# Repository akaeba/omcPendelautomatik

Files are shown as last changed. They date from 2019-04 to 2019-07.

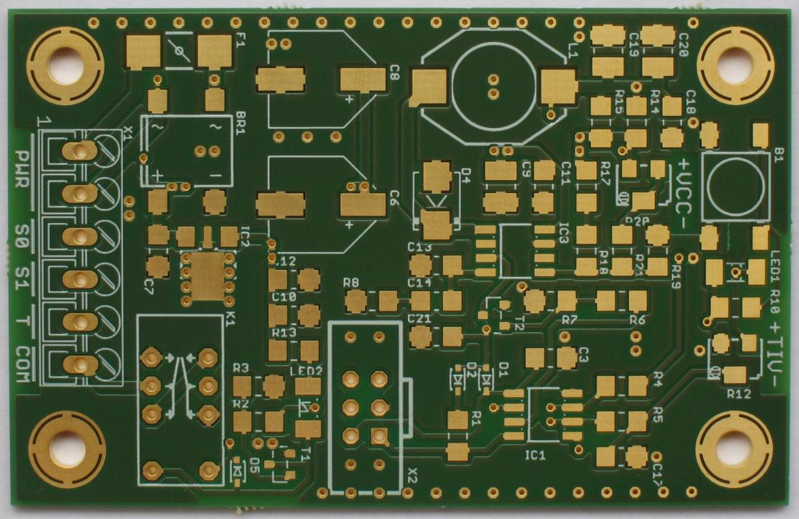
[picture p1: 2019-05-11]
98_pic/pcb_top.jpg

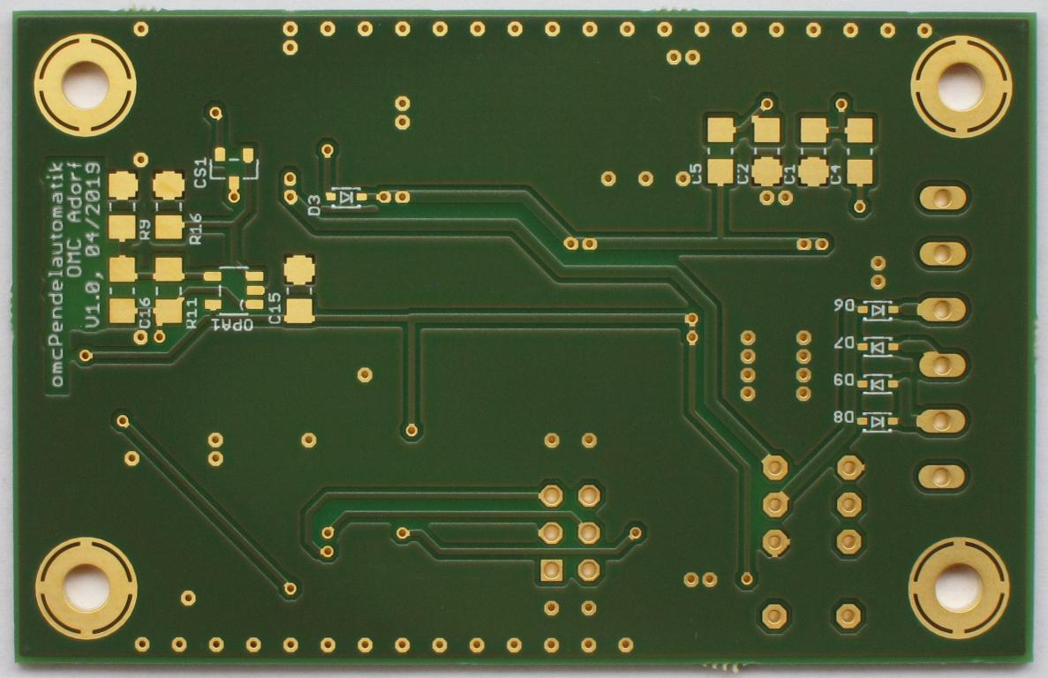
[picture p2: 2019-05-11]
98_pic/pcb_bottom.jpg

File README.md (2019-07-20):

# omcPendelautomatik
Circuit to drive a model train cyclic from one station to the other and back.

## Schematic

### Current Supervision

#### Current sensing and high-to-low conversion
The current sensor measures the voltage drop over an 0.5R shunt resistor. The high to low side voltage translation
is realized by [ZXCT1009](https://www.diodes.com/assets/Datasheets/ZXCT1009.pdf). According to the datasheet causes 
100mV voltage difference a output current of 1mA. Follows for V<sub>OUT</sub>:

V_{out} = I_{VCC} \cdot R_{SENSE}} \cdot \frac{1mA}{100mV} \cdot R_{out}

with R<sub>SENSE</sub>=0.5 and R<sub>OUT</sub>=200:

I_{VCC}[A]=V_{OUT}[V]

#### Opamp signal conditioning
The current sensors output voltage is processed by an band-limited operational amplifier

##### Amplification
The following can be noted as a starting point:

\Large -I_1=\frac{V_I}{R_1}
\Large I2=\frac{V_O-V_I}{R_2}
\Large 0=I_2-I_1

All three equations inserted into each other:

\Large \frac{V_O-V_I}{R_2}-\frac{V_I}{R_1}

For the amplification follows:

\Large V_O=V_I\Bigl(1+\frac{R_2}{R_1}\Bigr)

##### Band limit
A band limitation of the operational amplifier guarantees a good SNR and ADC resolution. An capacitor in parallel to R<sub>2</sub> limits the amplification.
The [Amplification](#Amplification) extended with an expression of the capacitive resistance follows:

\Large V_O=V_I\Bigl(1+\frac{R_2||\frac{1}{\omega C}}{R_1}\Bigr)

After short calculation and solving the parallel operator:

\Large V_O=V_I\Bigl(1+\frac{R_2}{R_1(1+\omega CR_2)}\Bigr)

Using the -3dB criteria

\frac{1}{\sqrt{2}}

Follows

\frac{1}{\sqrt{2}}=\frac{R_2}{R_1(1+\omega CR_2})

Solved for C

\boxed{C=\frac{\sqrt{2}R_2-R_1}{\omega R_1 R_2}}

## Used Tools
* Eagle 7.7

## Libraries
* Eagle:
    * [omcEagleLib](https://github.com/gallioleo/omcEagleLib)

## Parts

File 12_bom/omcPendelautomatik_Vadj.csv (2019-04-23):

Qty | Order | Distributor | Reference | VALUE | Description
1 | SMD 1/4W 0,0 | Reichelt | R17 | 0R | YAGEO RC1206 - General Purpose Chip Resistors
2 | X7R-G1206 100N | Reichelt | C15, C21 | 100n/50V | X7R Ceramic Capacitors
5 | X7R-G1206 100N | Reichelt | C3, C10, C11, C17, C18 | 100n/50V | X7R Ceramic Capacitors
1 | 44W-10K | Reichelt | R12 | 10K | Model 44 - Cermet Trimming Potentiometer - TT Electronics
3 | SMD 1/4W 10K | Reichelt | R2, R6, R9 | 10K | YAGEO RC1206 - General Purpose Chip Resistors
4 | X7R-G1206 10N | Reichelt | C1, C2, C4, C5 | 10n/50V | X7R Ceramic Capacitors
1 | X7R-G1210 10 | Reichelt | C9 | 10µ/35V | X7R Ceramic Capacitors
2 | VF 150/35 P-F | Reichelt | C6, C8 | 150µ/35V | Aluminum Electrolytic Capacitors
4 | SMD 1/4W 1,0K | Reichelt | R4, R5, R10, R13 | 1K | YAGEO RC1206 - General Purpose Chip Resistors
2 | SMD 1/4W 1,0 | Reichelt | R14, R15 | 1R | YAGEO RC1206 - General Purpose Chip Resistors
1 | SMD 1/4W 200 | Reichelt | R16 | 200R | YAGEO RC1206 - General Purpose Chip Resistors
1 | NPO-G1206 220P | Reichelt | C13 | 220p/50V | NP0 Surface-Mount Ceramic Multilayer Capacitors
1 | SMD 1/4W 22K | Reichelt | R1 | 22K | YAGEO RC1206 - General Purpose Chip Resistors
1 | X7R-G1206 22N | Reichelt | C14 | 22n/50V | X7R Ceramic Capacitors
1 | WSL 6G | Reichelt | X2 | 2X3 | Box Header 2X3
1 | NPO-G1206 2,2N | Reichelt | C16 | 2n2/50V | NP0 Surface-Mount Ceramic Multilayer Capacitors
2 | X7R-G1206 2,2/50 | Reichelt | C7, C12 | 2µ2/50V | X7R Ceramic Capacitors
1 | L-PISM 33µ | Reichelt | L1 | 33µ | PISM - SMD Power Inductors
1 | SMD 1/4W 39K | Reichelt | R11 | 39K | YAGEO RC1206 - General Purpose Chip Resistors
1 | SMD 1/4W 3,3K | Reichelt | R19 | 3K3 | YAGEO RC1206 - General Purpose Chip Resistors
1 | SMD 1/4W 47K | Reichelt | R18 | 47K | YAGEO RC1206 - General Purpose Chip Resistors
2 | X5R-G1210 47 | Reichelt | C19, C20 | 47µ/16V | X5R Ceramic Capacitors
2 | SMD 1/4W 4,7K | Reichelt | R8, R21 | 4K7 | YAGEO RC1206 - General Purpose Chip Resistors
1 | 44W-50K | Reichelt | R20 | 50K | Model 44 - Cermet Trimming Potentiometer - TT Electronics
2 | SMD 1/4W 56K | Reichelt | R3, R7 | 56K | YAGEO RC1206 - General Purpose Chip Resistors
1 | TS 78L05 ACY | Reichelt | IC2 | 7805 | STMicroelectronics - L78L - Positive voltage regulators
2 | BSS 138 SMD | Reichelt | T1, T2 | BSS138 | BSS 138 - N-Channel Logic Level Enhancement Mode Field Effect Transistor
1 | SMD DB1A70 | Reichelt | BR1 | DB102S | DIL Rechtifier - 1.0A Single-Phase Glass Passivated Bridge Rectifier
1 | TASTER 9314 | Reichelt | B1 | JTP1138/4.3 | TACT SWITCH - JTP 1138
1 | L 5970 D | Reichelt | IC3 | L5970D | STMicroelectronics - L5970D - Up to 1A step down switching regulator
1 | MBRS 240 SMD | Reichelt | D4 | MBRS240 | MBRS2X0 - 2A Schottky Power Rectifier
1 | MCP 6401T-E/OT | Reichelt | OPA1 | MCP6401 | MCP6401 - 1 MHz, 45 µA Op Amps - Microchip
1 | NA 05W K | Reichelt | K1 | NA-5V | Fujitsu NA - Minature Relay - 2 Poles - 1 to 2A
1 | PIC 12F675-I/SN | Reichelt | IC1 | PIC12F675 | PIC12F675 - 8-Pin FLASH-Based 8-Bit CMOS Microcontrollers
8 | PMEG 4010BEA NXP | Reichelt | D1, D2, D3, D5, D6, D7, D8, D9 | PMEG4010 | PMEGXX10 - 1A very low VF MEGA Schottky barrier rectifier - NXP
1 | AKL 086-06 | Reichelt | X1 | RT034 Typ 086 | Screw solder terminal - X06
1 | SMD-LED 1206 RT | Reichelt | LED1 | Red | LED Monochromatic
1 | OMT 125 0,5A | Reichelt | F1 | T 0A5 | OMT - Non resettable SMD Fuse
1 | SMD-LED 1206 GE | Reichelt | LED2 | Yellow | LED Monochromatic
1 | ZXCT 1009FTA | Reichelt | CS1 | ZXCT1009 | ZXCT1009 - HIGH-SIDE CURRENT MONITOR

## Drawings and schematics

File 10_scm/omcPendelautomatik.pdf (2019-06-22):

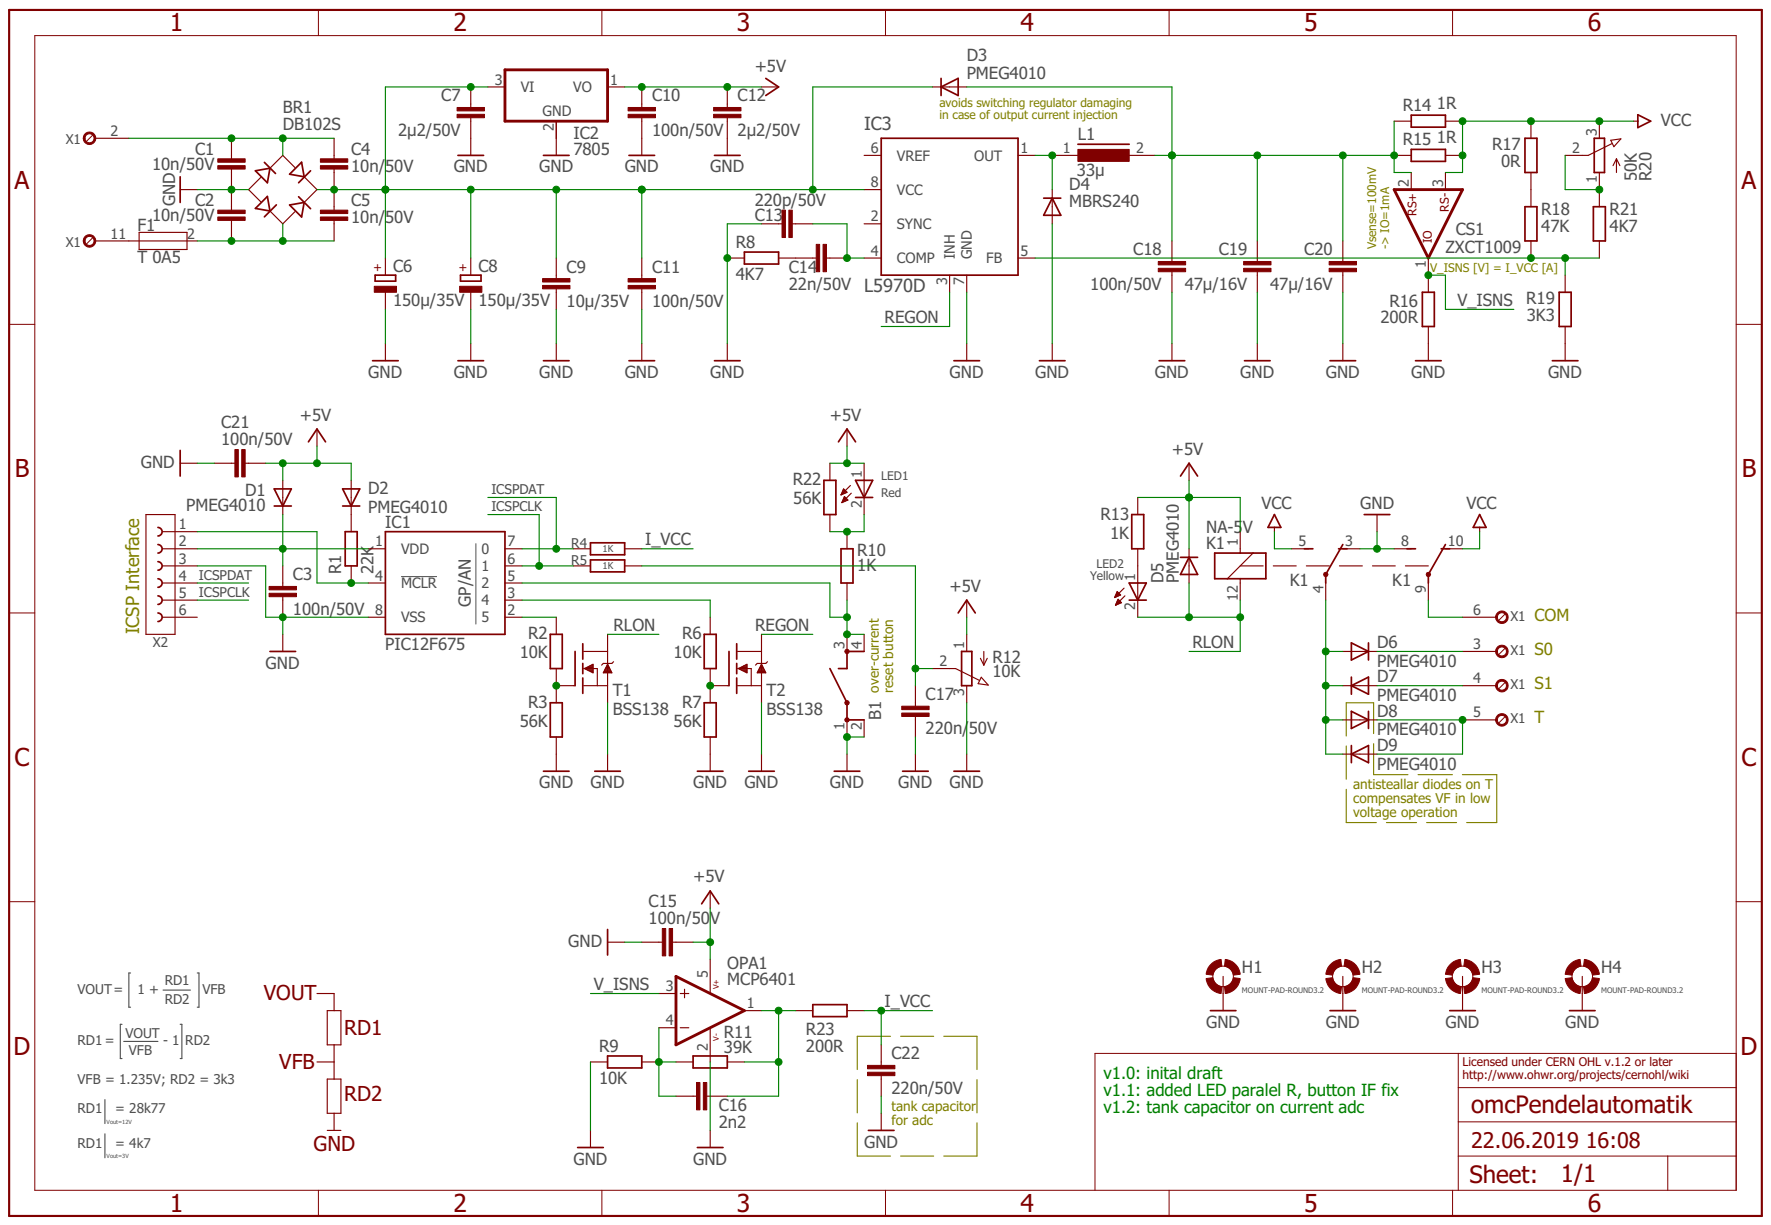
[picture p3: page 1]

avoids switching regulator damaging
in case of output current injection

over-current reset button tank capacitor

antisteallar diodes on T
compensates VF in low
voltage operation

Licensed under CERN OHL v.1.2 or later http://www.ohwr.org/projects/cernohl/wiki omcPendelautomatik

v1.1: added LED paralel R, button IF fix v1.0: inital draft v1.2: tank capacitor on current adc

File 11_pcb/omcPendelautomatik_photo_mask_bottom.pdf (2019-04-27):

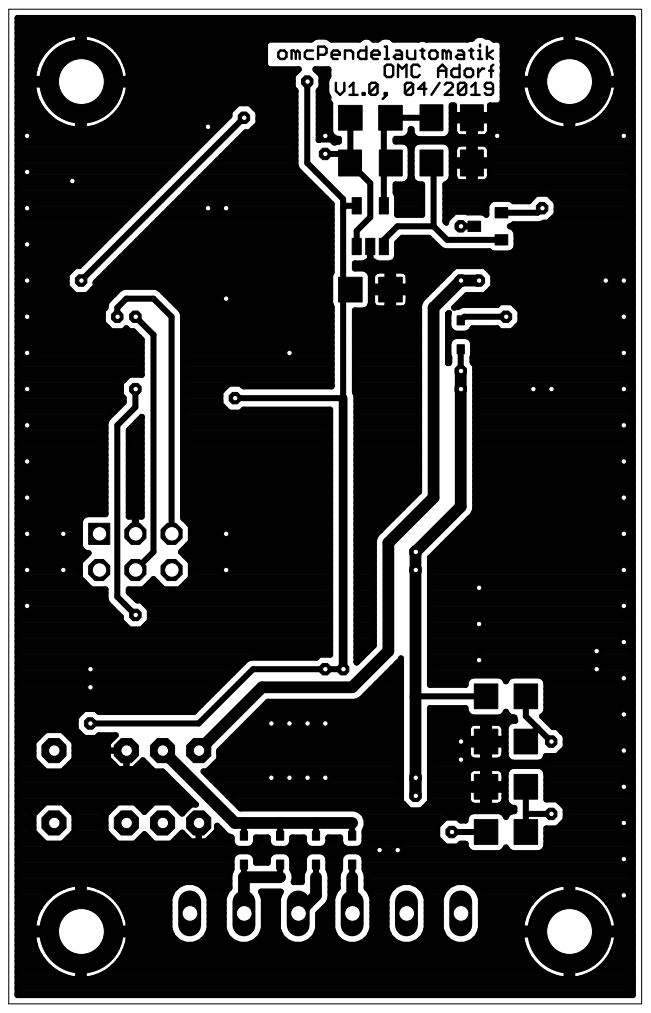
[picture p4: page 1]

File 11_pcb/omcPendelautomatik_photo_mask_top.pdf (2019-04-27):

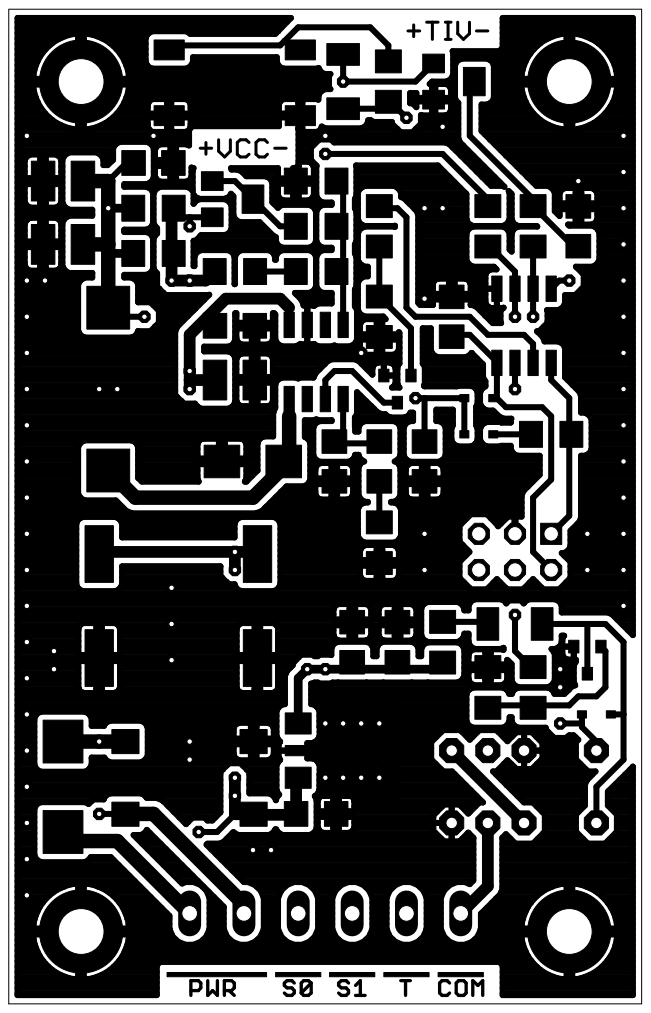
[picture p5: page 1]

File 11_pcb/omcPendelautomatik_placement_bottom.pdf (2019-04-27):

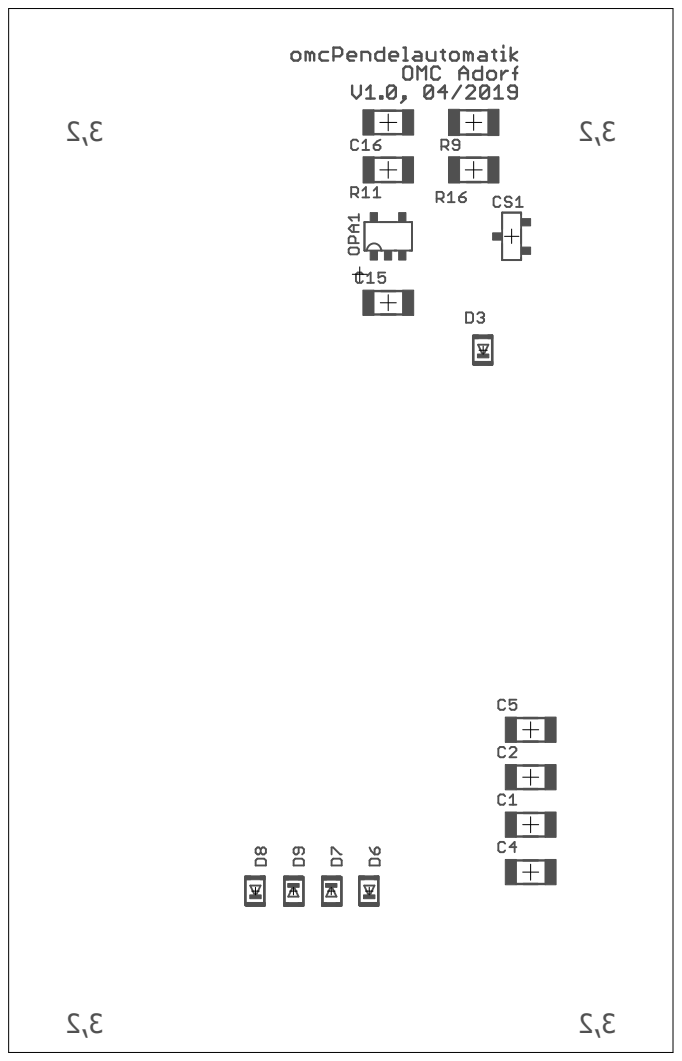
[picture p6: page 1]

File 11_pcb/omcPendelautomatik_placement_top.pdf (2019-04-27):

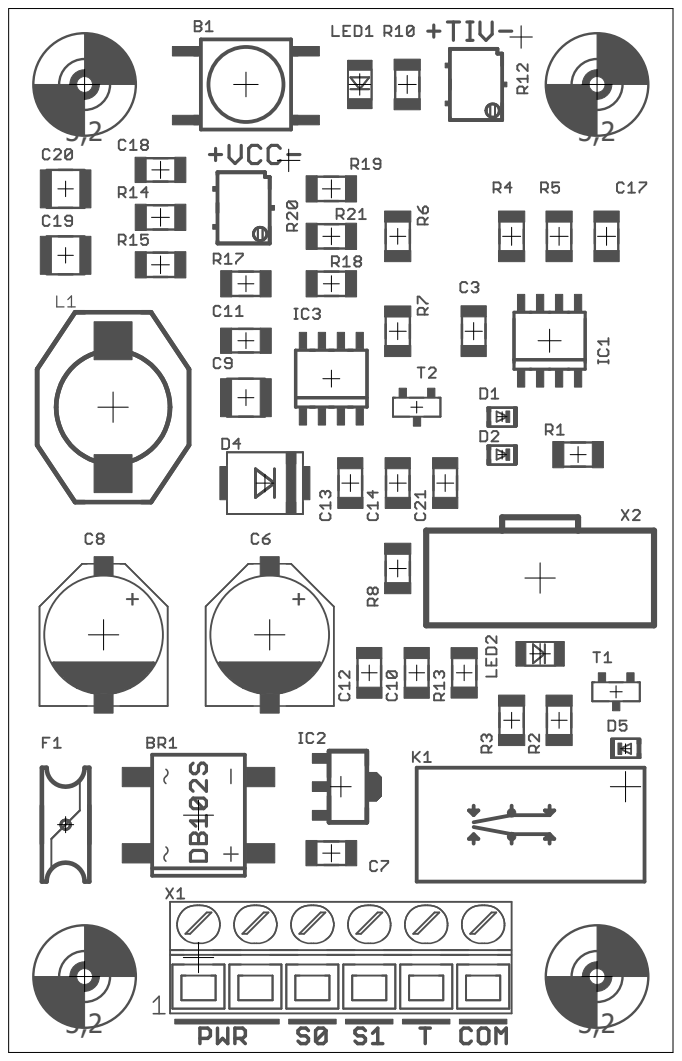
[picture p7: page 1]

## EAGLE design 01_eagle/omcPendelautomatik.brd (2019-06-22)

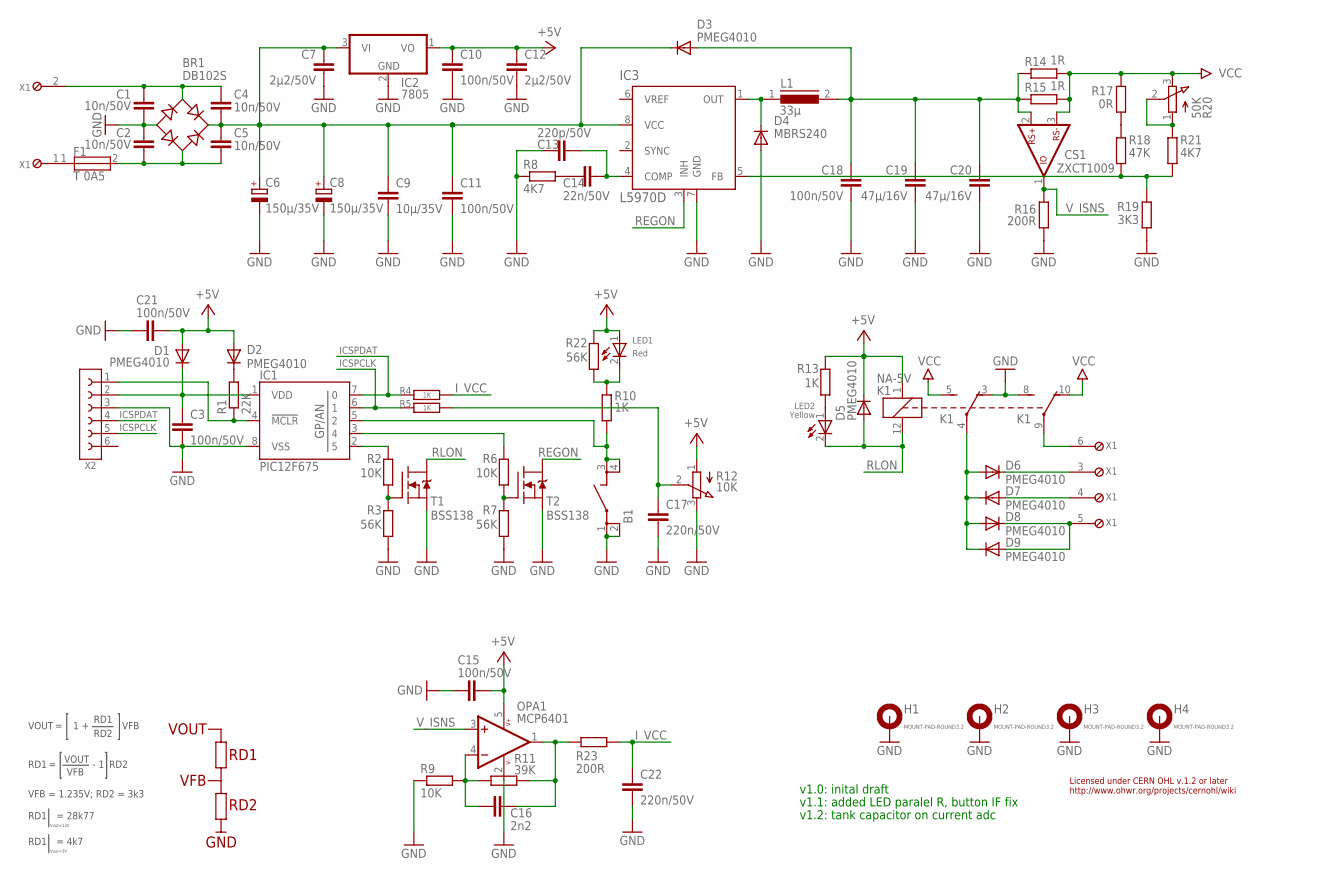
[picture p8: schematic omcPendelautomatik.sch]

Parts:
B1: JTP1138/4.3; SMD_X4_11X6
BR1: DB102S; DBS
C1, C2, C4, C5: 10n/50V; 1206
C3, C10, C11, C15, C18, C21: 100n/50V; 1206
C6, C8: 150µ/35V; PANF
C7, C12: 2µ2/50V; 1206
C9: 10µ/35V; 1210
C13: 220p/50V; 1206
C14: 22n/50V; 1206
C16: 2n2; 1206
C17, C22: 220n/50V; 1206
C19, C20: 47µ/16V; 1210
CS1: ZXCT1009; SOT23
D1, D2, D3, D5, D6, D7, D8, D9: PMEG4010; SOD323
D4: MBRS240; DO214AA
F1: T 0A5; OMT125
H1, H2, H3, H4: MOUNT-PAD-ROUND3.2; 3,2-PAD
IC1: PIC12F675; SOIC08
IC2: 7805; SOT89W
IC3: L5970D; SOIC08
K1: NA-5V; THT_5M08M_5M08M_2M54M
L1: 33µ; PISM
LED1: Red; LED3216
LED2: Yellow; LED3216
OPA1: MCP6401; SOT23-5
R1: 22K; 1206
R2, R6, R9: 10K; 1206
R3, R7, R22: 56K; 1206
R4, R5, R10, R13: 1K; 1206
R8, R21: 4K7; 1206
R11: 39K; 1206
R12: 10K; TTM44W
R14, R15: 1R; 1206
R16, R23: 200R; 1206
R17: 0R; 1206
R18: 47K; 1206
R19: 3K3; 1206
R20: 50K; TTM44W
T1, T2: BSS138; SOT23
X1: RT034 Typ 086; RT03406T086
X2: 2X3; BOXHD-06-2.54-S

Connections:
+5V: C10.1, C12.1, C15.2, C21.2, D1.A, D2.A, D5.C, IC2.1 (VO), K1.1 (2), LED1.1 (A), OPA1.5 (V+), R12.1 (A), R13.2, R22.2
GND: B1.1, B1.2, BR1.-, C1.2, C2.1, C3.2, C6.CN (-), C7.2, C8.CN (-), C9.2, C10.2, C11.2, C12.2, C13.1, C15.1, C17.2, C18.2, C19.2, C20.2, C21.1, C22.2, D4.A, H1.B3,2, H2.B3,2, H3.B3,2, H4.B3,2, IC1.8 (VSS), IC2.2 (GND), IC2.4 (GND), IC3.7 (GND), K1.3 (O), K1.8 (S), OPA1.2 (V-), R3.1, R7.1, R8.1, R9.1, R12.3 (E), R16.1, R19.1, T1.2 (S), T2.2 (S), X2.3
ICSPCLK: IC1.6 (1), R5.1, X2.5
ICSPDAT: IC1.7 (0), R4.1, X2.4
I_VCC: C22.1, R4.2, R23.1
unnamed: D4.C, IC3.1 (OUT), L1.1
unnamed: R20.1 (A), R20.2 (S), R21.2
unnamed: C13.2, C14.1, IC3.4 (COMP)
unnamed: C14.2, R8.2
unnamed: R2.1, R3.2, T1.1 (G)
unnamed: BR1.+, C4.2, C5.1, C6.CP (+), C7.1, C8.CP (+), C9.1, C11.1, D3.C, IC2.3 (VI), IC3.8 (VCC)
unnamed: C3.1, D1.C, IC1.1 (VDD), X2.2
unnamed: F1.1, X1.1
unnamed: IC3.5 (FB), R18.1, R19.2, R21.1
unnamed: IC1.4 (!MCLR!), R1.1, X2.1
unnamed: D2.C, R1.2
unnamed: IC1.2 (5), R2.2
unnamed: R6.1, R7.2, T2.1 (G)
unnamed: IC1.3 (4), R6.2
unnamed: LED2.1 (A), R13.1
unnamed: R17.1, R18.2
unnamed: BR1.AC1, C1.1, C4.1, X1.2
unnamed: D6.C, X1.3
unnamed: C17.1, R5.2, R12.2 (S)
unnamed: C16.1, OPA1.4 (-IN), R9.2, R11.1
unnamed: D7.A, X1.4
unnamed: D6.A, D7.C, D8.A, D9.C, K1.4
unnamed: BR1.AC2, C2.2, C5.2, F1.2
unnamed: K1.9, X1.6
unnamed: B1.3, B1.4, IC1.5 (2), R10.1
unnamed: D8.C, D9.A, X1.5
unnamed: LED1.2 (C), R10.2, R22.1
unnamed: C16.2, OPA1.1 (OUT), R11.2, R23.2
REGON: IC3.3 (INH), T2.3 (D)
RLON: D5.A, K1.12 (1), LED2.2 (C), T1.3 (D)
VCC: CS1.3 (-RS), K1.5 (S), K1.10 (O), R14.2, R15.2, R17.2, R20.3 (E)
VOUT: C18.1, C19.1, C20.1, CS1.2 (+RS), D3.A, L1.2, R14.1, R15.1
V_ISNS: CS1.1 (IOUT), OPA1.3 (+IN), R16.2

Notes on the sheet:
GND
VFB
VOUT
RD1
RD2
1 +
VFB = 1.235V; RD2 = 3k3
= 28k77
- 1
Vout=12V
= 4k7
Vout=3V
Licensed under CERN OHL v.1.2 or later http://www.ohwr.org/projects/cernohl/wiki
v1.1: added LED paralel R, button IF fix
v1.0: inital draft
v1.2: tank capacitor on current adc

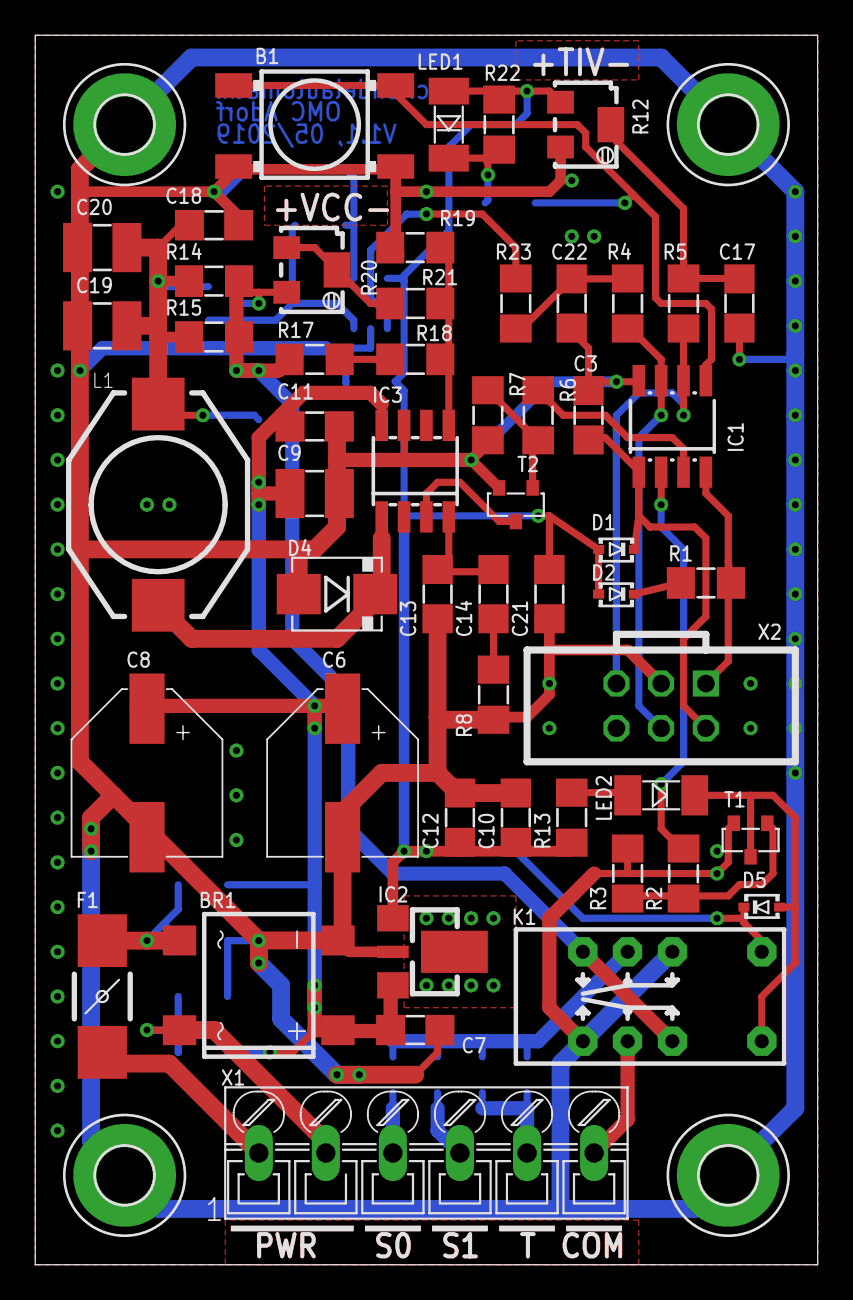
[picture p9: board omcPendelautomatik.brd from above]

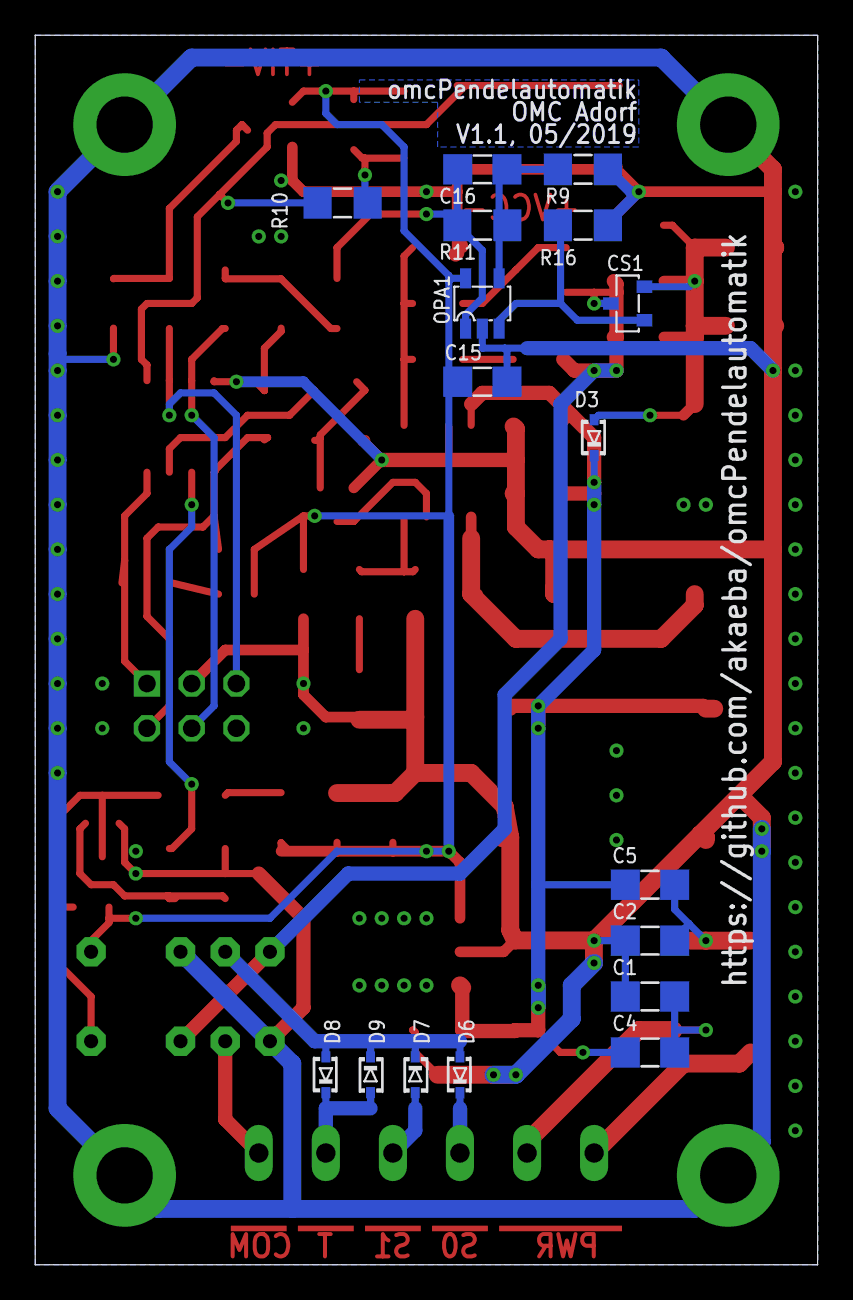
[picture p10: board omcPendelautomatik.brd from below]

Board: 2 copper layers, 44.5 x 69.8 mm, 74 parts (17 on the bottom side), 38 nets.

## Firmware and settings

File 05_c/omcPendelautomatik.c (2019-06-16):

/******************************************************************************
*  @copyright  GPLv3
*  Company     OMC Adorf
*  Address     Markt 35b, 08626 Adorf
*
*  @file       omcPendelautomatik.c
*  @author     Andreas Kaeberlein <andreas.kaeberlein@web.de>
*  @date       May 2, 2019
*  @version    1.0
*
*  @brief      FW Pendelautomatik
*
*  Implements behaviour Pendelautomatik
*
*******************************************************************************/


/** Includes **/
/* standard libs */
#include <stdint.h>
/* self */
#include "omcPendelautomatik.h"



/**
 *  mcu_init
 *    intializes MCU, port, timers, adcs...
 */
int mcu_init()
{
    /* Configure IO */
    GPIO   = 0;                       // all GPIOs drive zero
    GPIO   |= GP2;                    // Red OC LED is off
    TRISIO = IO_ALL_INPUT;            // All IOs are Input
    TRISIO &= ~(TRISIO4 | TRISIO5);   // GPIO4/5 is output

    /* Configure ADC */
    ADCON0 = 0;                           // prepare for OR
    ADCON0 |= (ADC_ADFM_LEFT << ADFM);    // ADC word alignment
    ADCON0 |= (ADC_VCFG_VDD << VCFG);     // ADC reference is VDD
    ANSEL  = 0;                           // clear register
    ANSEL  |= ( ANS0 | ANS1 );            // GP0 and GP1 analog input
    ANSEL  |= ADC_FOSC_64;                // Tconv = 64 * 1 / 8 MHz = 8us
    ADRESH = 0;                           // clear
    ADRESL = 0;                           //
     
    /* configure timer0 for 1ms interrupt */
    TMR0       = 0;         // clear timer
    OPTION_REG &= ~T0CS;    // Internal instruction cycle clock (CLKOUT)
    OPTION_REG |= PSA;      // Prescaler is assigned to the WDT
     
    /* configure IRQ */
    INTCON = 0;        // all interrupts disable
    INTCON |= T0IE;    // timer0 interrupt enable, required for 1ms timing normal
    INTCON |= GIE;     // all unmasked IRQ enabled
     
    /* gracefull end */
    return 0;
}



/**
 *  handle_init
 *    intializes common used storage handle
 */
int handle_init(tOmcPendelautomatik *self)
{
    /* init variable */
    self->uint8TmrDiv = 0;
    self->int16TmrFrac = 0;
    self->uint32Time_ms = 0;
    self->uint8AdcBuf0[0] = 0;
    self->uint8AdcBuf0[1] = 0;
    self->uint8AdcBuf0[2] = 0;
    self->uint8AdcBuf1[0] = 0;
    self->uint8AdcBuf1[1] = 0;
    self->uint8AdcBuf1[2] = 0;
    self->uint8CurIL = 0;
    self->uint8CurTi = 0;

    /* gracefull end */
    return 0;
}



/**
 *  shift_value
 *    shift value one position down in array
 */
int shift_value(uint8_t val[], uint8_t len)
{
    /** Variables **/
    uint8_t    i;    // iterator
    
    /* shift value down */
    for ( i = 1; i < len; ++i ) {
        val[i] = val[i-1];
    }
    
    /* gracefull end */
    return 0;
}



/**
 *  interrupt
 *    interrupt service routine
 */
void interrupt(tOmcPendelautomatik *self)
{
    /* disable all unmasked interrupt */
    INTCON &= ~GIE;
    
    /* TMR0 IRQ? */
    if ( INTCON.T0IF ) {
        /* IRQ Flag */
        INTCON &= ~T0IF;    // clear interupt flag
        
        /* 1ms Timing Normal 
         * TMR0 (8bit) used, IRQ at overflow 0xFF -> 0x00
         * FOSC 8MHz
         * (1ms / ( (1 / 8 MHz) * TMR0 * 4 ) ) = 7,8125
         */
        self->uint8TmrDiv = self->uint8TmrDiv + 1;
        if ( (self->uint8TmrDiv == 7) && (self->int16TmrFrac >= 0) ) {
            self->uint8TmrDiv = 0;
            self->int16TmrFrac = self->int16TmrFrac - 8125;
            self->uint32Time_ms = self->uint32Time_ms + 1;
        } else if ( (self->uint8TmrDiv == 8) && (self->int16TmrFrac < 0) ) {
            self->uint8TmrDiv = 0;
            self->int16TmrFrac = self->int16TmrFrac + 1875;
            self->uint32Time_ms = self->uint32Time_ms + 1;
        }
        
        /* handle adc */
        if ( ! ADCON0.GO_NOT_DONE ) {
             /* Last Conversion from Chn0 performed 
              *   -> used for current measurement
              */
             if ( (ADCON0 & ADC_CHN_MSK) == ADC_CHN_0 ) {
                 /* update average current value */
                 self->uint16Temp = self->uint8AdcBuf0[0] + self->uint8AdcBuf0[1] + self->uint8AdcBuf0[2] + ADRESH;  // avearage with last four values
                 self->uint8CurIL = (uint8_t) (self->uint16Temp >> 2);                                               // four values, bit shift 2 for div4
                 shift_value(self->uint8AdcBuf0, sizeof(self->uint8AdcBuf0) / sizeof(self->uint8AdcBuf0[0]));        // drop last element
                 self->uint8AdcBuf0[0] = ADRESH;                                                                     // store current adc value
                 /* change input and start next conversion */
                 ADCON0 |= ADC_CHN_1;      // select Channel 1 as new analog input, prepare for time measurement
                 ADCON0 |= GO_NOT_DONE;    // start new conversion
                 
             /* Last Conversion from Chn1 performed 
              *   -> used for cycle time
              */
             } else if ( (ADCON0 & ADC_CHN_MSK) == ADC_CHN_1 ) {
                 /* update average current value */
                 self->uint16Temp = self->uint8AdcBuf1[0] + self->uint8AdcBuf1[1] + self->uint8AdcBuf1[2] + ADRESH;  // avearage with last four values
                 self->uint8CurTi = (uint8_t) (self->uint16Temp >> 2);                                               // four values, bit shift 2 for div4
                 shift_value(self->uint8AdcBuf1, sizeof(self->uint8AdcBuf1) / sizeof(self->uint8AdcBuf1[0]));        // drop last element
                 self->uint8AdcBuf1[0] = ADRESH;                                                                     // store current adc value
                 /* change input and start next conversion */
                 ADCON0 &= ~ADC_CHN_1;     // select Channel 0 as new analog input, prepare for current meas
                 ADCON0 |= GO_NOT_DONE;    // start new conversion
             }
        }
    }
    
    /* enable all unmasked IRQ */
    INTCON |= GIE;
}



/**
 *  wait_50ms
 *    waits 50ms
 */
int wait_50ms()
{
    delay_ms(50);
    return 0;
}



/**
 *  wait_500ms
 *    waits 500ms
 */
int wait_500ms()
{
    /** Variables **/
    uint8_t       i;
    
    /* call 50ms wait functions */
    for ( i = 0; i < 10; i++ ) {
        wait_50ms();
    }
    
    /* normal end */
    return 0;
}



/**
 *  handle_oc
 *    handles over current case, polls clear button
 */
int handle_oc()
{
     /** Variables */
     uint8_t   uint8ButtonNew = 1;
     uint8_t   uint8ButtonOld = 1;
     
     
      /* poll loop, over current clear button */
      while ( (uint8ButtonNew != uint8ButtonOld) && (uint8ButtonNew != 0) ) {
          /* read-out switch */
          TRISIO |= TRISIO2;                     // input
          delay_ms(1);                           // wait 1ms
          uint8ButtonOld = uint8ButtonNew;       // capture old value
          uint8ButtonNew = BUTTON_OC;            // read out value
          /* red LED */
          TRISIO &= ~TRISIO2;                    // output
          XLED_RED = OFF;                        // LED on
          delay_ms(9);                           // wait 9ms, 90% lumicity
      }
     
     /* graceful end */
     return 0;
}



/**
 *  main
 *    entry point
 */
int main() 
{
     /** Variables **/
     tOmcPendelautomatik myHandle;
     
     
     /* init */
     mcu_init();               // MCU
     handle_init(&myHandle);   // common storage element
     
     /* start cycling */
     IO_REG = ON;       // switch power supply on
     IO_RELAY = ON;     // switch relay on
     
     /* infinite loop */
     while(1) {
         /* check for direction change */
         if ( myHandle.uint32Time_ms > (UI_TIME_DIG_MS * myHandle.uint8CurTi) ) {
             myHandle.uint32Time_ms = 0;               // clear current time
             IO_REG = OFF;                             // disable regulator
             wait_50ms();                              // wait for regulator shutdown
             IO_RELAY = IO_RELAY ^ 0x1;                // toggle direction
             wait_50ms();                              // wait for relay
             IO_REG = ON;                              // enable power
         }
         
         /* check for over current */
         if ( myHandle.uint8CurTi > 25 ) {             // ToDO
             IO_REG = OFF;                             // stop current flow
             if ( 0 != handle_oc() ) {
                while(1) {                             // stuck finally, red LED blinks, leave with POR
                    IO_RELAY = OFF;
                    XLED_RED = OFF;
                    wait_500ms();
                    XLED_RED = ON;
                    wait_500ms();
                }
             }
             myHandle.uint32Time_ms = 0;               // clear current time, go one normally
             IO_REG = ON;                              // restore power supply
         }
     }
     
     /* graceful end */
     return 0;
}

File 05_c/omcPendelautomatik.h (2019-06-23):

/******************************************************************************
*  @copyright  GPLv3
*  Company     OMC Adorf
*  Address     Markt 35b, 08626 Adorf
*
*  @file       omcPendelautomatik.h
*  @author     Andreas Kaeberlein <andreas.kaeberlein@web.de>
*  @date       May 2, 2019
*  @version    1.0
*
*  @brief      FW Pendelautomatik
*
*  Implements behaviour Pendelautomatik
*
*******************************************************************************/


// Define Guard
#ifndef __OMC_PENDELAUTOMATIK_H
#define __OMC_PENDELAUTOMATIK_H

/**
 *  @defgroup CMACRO
 *  help macros for pre compiler
 *  @{
 */
#define pwrtwo(x) (1 << (x))
/** @} */   // CMACRO


/**
 *  @defgroup Help
 *  help defines
 *  @{
 */
#define UI_TIME_MIN_SEC      5                                                            /**<  UI: Minimal Time between direction change */
#define UI_TIME_MAX_SEC      180                                                          /**<  UI: Maximum Time between direction change */
#define UI_TIME_DIG_MS       (((UI_TIME_MAX_SEC - UI_TIME_MIN_SEC) * 1000 ) / pwrtwo(8))  /**<  UI: Time increment per measured digit     */
#define UI_OC_TRIP_MA        300                                                          /**<  UI: Fence for over current tripping       */
//#define UI_OC_TRIP_DIG

/** @} */   // UI


/**
 *  @defgroup ADC
 *  configures and controls the ADC
 *  @{
 */
#define ADC_FOSC_64     ( ADCS2 | ADCS1 )         /**<  ADC: Clock Divider =64, applied on ANSEL            */
#define ADC_CHN_IDX     2                         /**<  ADC: Analog Channel Select bits                     */
#define ADC_CHN_MSK     ( CHS1 | CHS0 )           /**<  ADC: sel channel selection bits, applied on ADCON   */
#define ADC_CHN_0       ( 0 << ADC_CHN_IDX )      /**<  ADC: Channel 00 (AN0)                               */
#define ADC_CHN_1       ( 1 << ADC_CHN_IDX )      /**<  ADC: Channel 01 (AN1)                               */
#define ADC_CHN_2       ( 2 << ADC_CHN_IDX )      /**<  ADC: Channel 02 (AN2)                               */
#define ADC_CHN_3       ( 3 << ADC_CHN_IDX )      /**<  ADC: Channel 03 (AN3)                               */
#define ADC_ADFM_LEFT   0                         /**<  ADC: A/D Result Formed, Left justified              */
#define ADC_ADFM_RIGHT  1                         /**<  ADC: A/D Result Formed, Right justified             */
#define ADC_VCFG_VREF   1                         /**<  ADC: Voltage Reference bit, VREF pin                */
#define ADC_VCFG_VDD    0                         /**<  ADC: Voltage Reference bit, VDD pin                 */
/** @} */   // ADC



/**
 *  @defgroup IO
 *  GPIO port control
 *  @{
 */
#define IO_ALL_INPUT ( TRISIO0 | TRISIO1 | TRISIO2 | TRISIO3 | TRISIO4 | TRISIO5 )     /**<  IO: GPIO pin configured as an input (tri-stated) */
#define IO_RELAY     GPIO.B5                                                           /**<  IO: Port Connected to Relay                      */
#define ON           1                                                                 /**<  IO: Relay is active                              */
#define OFF          0                                                                 /**<  IO: Relay is inactive                            */
#define IO_REG       GPIO.B4                                                           /**<  IO: Port Connected to Regulator                  */
#define XLED_RED     GPIO.B2                                                           /**<  IO: Feeds low active red LED                     */
#define BUTTON_OC    GPIO.B2                                                           /**<  IO: Reeds Over-current clear button out          */

/** @} */   // IO



/**
 *  @typedef tOmcPendelautomatik
 *
 *  @brief  data handle
 *
 *  programs data handle
 *
 *  @since  May 28, 2019
 *  @author Andreas Kaeberlein
 */
typedef struct tOmcPendelautomatik {
    uint8_t     uint8TmrDiv;               /**< divids from TMR0 IRQ to 1ms  */
    int16_t     int16TmrFrac;              /**< handles fracs to achieve MS  */
    uint32_t    uint32Time_ms;             /**< Time in ms steps             */
    uint8_t     uint8AdcBuf0[3];           /**< avering buffer for ADC input */
    uint8_t     uint8AdcBuf1[3];           /**< avering buffer for ADC input */
    uint16_t    uint16Temp;                /**< temporary variable           */
    uint8_t     uint8CurIL;                /**< current load current         */
    uint8_t     uint8CurTi;                /**< current cyclic time          */

} tOmcPendelautomatik;


/* C++ compatibility */
#ifdef __cplusplus
extern "C"
{
#endif // __cplusplus


/**
 *  @brief MCU init
 *
 *  intializes MCU, port, timers, adcs...
 *
 *  @retval         0                   OK
 *  @since          2019-06-16
 *  @author         Andreas Kaeberlein
 */
int mcu_init();


/**
 *  @brief init data handle
 *
 *  intializes common used storage handle
 *
 *  @param[in,out]  this                storage element
 *  @retval         0                   OK
 *  @since          2019-06-16
 *  @author         Andreas Kaeberlein
 */
int handle_init(tOmcPendelautomatik *self);


/**
 *  @brief shift value in array
 *
 *  shift value one position down in array
 *
 *  @param[in,out]  val                 array with values
 *  @param[in]      len                 length of provided array
 *  @return         int                 state
 *  @retval         0                   OK
 *  @since          2019-06-16
 *  @author         Andreas Kaeberlein
 */
int shift_value(uint8_t val[], uint8_t len);


/**
 *  @brief interrupt
 *
 *  interrupt service routine
 *
 *  @param[in,out]  this                storage element
 *  @since          2019-06-16
 *  @author         Andreas Kaeberlein
 */
void interrupt(tOmcPendelautomatik *self);


/** 
 *  @brief 50ms wait
 *
 *  calls prmitive routine to wait 50ms
 *
 *  @return         int                 state
 *  @retval         0                   OK
 *  @since          2019-06-16
 *  @author         Andreas Kaeberlein
 */
int wait_50ms();


/**
 *  @brief 500ms wait
 *
 *  calls wait_50ms routine and builds up 500ms wait
 *
 *  @return         int                 state
 *  @retval         0                   OK
 *  @since          2019-06-16
 *  @author         Andreas Kaeberlein
 */
int wait_500ms();


/**
 *  @brief handle_oc
 *
 *  handles over current case, polls clear button
 *
 *  @return         int                 state
 *  @retval         0                   OK
 *  @since          2019-06-16
 *  @author         Andreas Kaeberlein
 */
int handle_oc();


#ifdef __cplusplus
}
#endif // __cplusplus

#endif  // __OMC_PENDELAUTOMATIK_H

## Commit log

2019-04-01 omcPendelautomatik.sch -> intermediate commit, due architecture change
    [omcPendelautomatik.sch]
2019-04-07 omcPendelautomatik.sch -> intermediate commit -> changed from '555' timing normal to 'uC'
    [omcPendelautomatik.sch]
2019-04-11 omcPendelautomatik.sch -> initial draft schematic finished
    [omcPendelautomatik.sch]
2019-04-19 omcPendelautomatik -> Placement and routing main parts done -> schematic changes for routing
    [omcPendelautomatik.brd, omcPendelautomatik.sch]
2019-04-19 omcPendelautomatik.brd -> adjust silk print on top side
    [omcPendelautomatik.brd]
2019-04-21 omcPendelautomatik.brd -> adjust bottom side silk
    [omcPendelautomatik.brd]
2019-04-21 omcPendelautomatik -> symbol update -> added some vias to connect top/bottom ground plane
    [omcPendelautomatik.brd, omcPendelautomatik.sch]
2019-04-22 omcPendelautomatik.brd -> added Polygon to avoid thermals at linear regulator
    [omcPendelautomatik.brd]
2019-04-22 omcPendelautomatik.brd -> adjust cap to avoid DRC error
    [omcPendelautomatik.brd]
2019-04-22 omcPendelautomatik_tapein.brd -> removed GND net and recalculated with ratsnest
    [omcPendelautomatik_tapein.brd]
2019-04-22 omcPendelautomatik -> added label with name and version
    [omcPendelautomatik.brd, omcPendelautomatik_tapein.brd]
2019-04-22 omcPendelautomatik -> adjusted Ref Desg. for manufacturing
    [omcPendelautomatik.brd, omcPendelautomatik_tapein.brd]
2019-04-23 omcPendelautomatik_Vadj -> added bom for adjustable voltage
    [omcPendelautomatik_Vadj.csv]
2019-04-24 omcPendelautomatik_Vadj.txt -> corrected BOM entry
2019-04-24 omcPendelautomatik_Vadj-Reichelt.csv -> added order card for reichelt
    [omcPendelautomatik_Vadj-Reichelt.csv]
2019-05-11 PCB pics
2019-05-26 bugfix uC button wiring
    [omcPendelautomatik.brd, omcPendelautomatik.sch, omcPendelautomatik_tapein.brd]
2019-06-15 omcPendelautomatik.sch -> added tank capacitor for current sense adc
    [omcPendelautomatik.sch]
2019-06-16 omcPendelautomatik -> initial draft w/o any test
    [omcPendelautomatik.cfg]
2019-06-22 added tank caps for current sense adc, pcb done
    [omcPendelautomatik.brd, omcPendelautomatik.sch]
2019-06-23 static divider by cmacro pow calc replaced
    [omcPendelautomatik.h]
2019-07-20 current transfer function

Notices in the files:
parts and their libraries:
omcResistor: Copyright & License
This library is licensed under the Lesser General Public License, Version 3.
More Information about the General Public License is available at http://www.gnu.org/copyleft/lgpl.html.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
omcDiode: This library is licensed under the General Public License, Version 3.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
